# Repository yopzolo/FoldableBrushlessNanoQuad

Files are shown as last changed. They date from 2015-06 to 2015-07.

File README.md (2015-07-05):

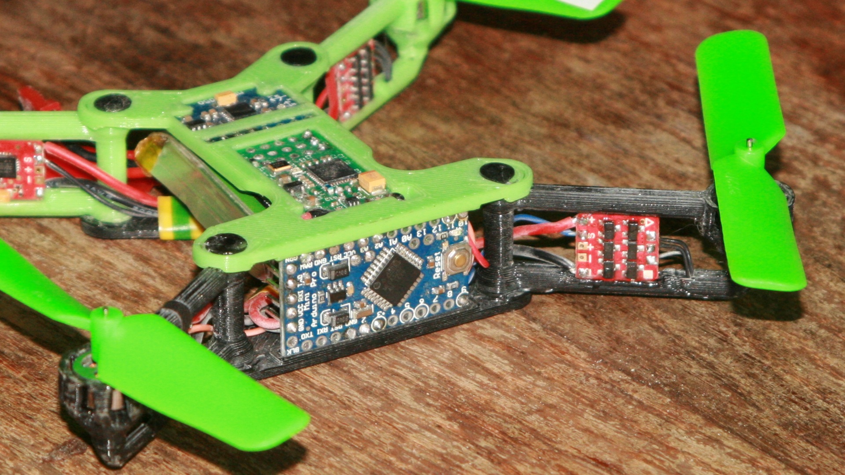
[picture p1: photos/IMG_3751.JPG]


## BOM
* [Arduino uno 3.3V / 8MHz](http://www.amazon.fr/gp/product/B00KMMF4TI?psc=1&redirect=true&ref_=oh_aui_detailpage_o07_s00)
* [MPU6050](http://www.amazon.fr/gp/product/B00E1EQXL6?psc=1&redirect=true&ref_=oh_aui_detailpage_o03_s00)
* [R410X](https://www.hobbyking.com/hobbyking/store/uh_customerShowOrderDetails2.asp?idOrder=20011845025)
* 4 X [Mi-3A](https://www.hobbyking.com/hobbyking/store/__44697__SuperMicro_Systems_Brushless_ESC_3A_Mi_3A.html)
* 4 X [hexTronik 2 gram Brushless Outrunner 7700kv](https://www.hobbyking.com/hobbyking/store/__7230__hexTronik_2_gram_Brushless_Outrunner_7700kv.html)
* 3020 propellers ( [Vl](https://www.hobbyking.com/hobbyking/store/%5F%5F40028%5F%5F3020%5FPropellers%5FGreen%5FL%5FH%5FRotation%5F5Pcs%5FBag%5F.html) [Vr](https://www.hobbyking.com/hobbyking/store/%5F%5F40029%5F%5F3020R%5FPropellers%5FGreen%5FR%5FH%5FRotation%5F5Pcs%5FBag%5F.html) [Or](https://www.hobbyking.com/hobbyking/store/%5F%5F41096%5F%5F3020R%5FPropellers%5FOrange%5FR%5FH%5FRotation%5F5Pcs%5FBag%5F.html) [Ol](https://www.hobbyking.com/hobbyking/store/%5F%5F41095%5F%5F3020%5FPropellers%5FOrange%5FL%5FH%5FRotation%5F5Pcs%5FBag%5F.html) [Br](https://www.hobbyking.com/hobbyking/store/%5F%5F40027%5F%5F3020R%5FPropellers%5FBlack%5FR%5FH%5FRotation%5F5Pcs%5FBag%5F.html) [Bl](https://www.hobbyking.com/hobbyking/store/%5F%5F40026%5F%5F3020%5FPropellers%5FBlack%5FL%5FH%5FRotation%5F5Pcs%5FBag%5F.html) )
* Silicon Wire [Black](https://www.hobbyking.com/hobbyking/store/%5F%5F10936%5F%5FTurnigy%5FPure%5FSilicone%5FWire%5F24AWG%5F1mtr%5FBlack.html) [Red](https://www.hobbyking.com/hobbyking/store/%5F%5F10937%5F%5FTurnigy%5FPure%5FSilicone%5FWire%5F24AWG%5F1mtr%5FRed.html)
* Batteries ( 1S < 20g ) - [300mAh](https://www.hobbyking.com/hobbyking/store/%5F%5F20384%5F%5FTurnigy%5Fnano%5Ftech%5F300mah%5F1S%5F35%5F70C%5FLipo%5FPack%5FFits%5FNine%5FEagles%5FSolo%5FPro%5F100%5F.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) [750mAh](https://www.hobbyking.com/hobbyking/store/%5F%5F20386%5F%5FTurnigy%5Fnano%5Ftech%5F750mah%5F1S%5F35%5F70C%5FLipo%5FPack%5FFits%5FNine%5FEagles%5FSolo%5FPro%5F180%5F.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)

# Calibrating and Printing

## micro_quad_brushless.scad needs 3 files

* constants.scad - printer constants
* components.scad - electronic component mocks
* componentsTest.scad - display and print test stubs for electronics and motors

## Adjust the params to fit your printer and electronic components

0. adjust printer constants
0. adjust electronic component mocks
0. render, export, slice, print and test with componentsTest.scad

## Reposition electronic components
if new size made them out of bound you must edit the copter frame micro_quad_brushless.scad to Reposition them

## Print
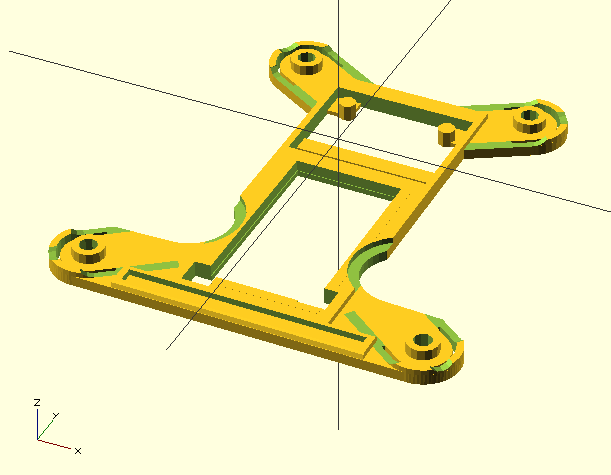
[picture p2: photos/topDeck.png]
Top Deck

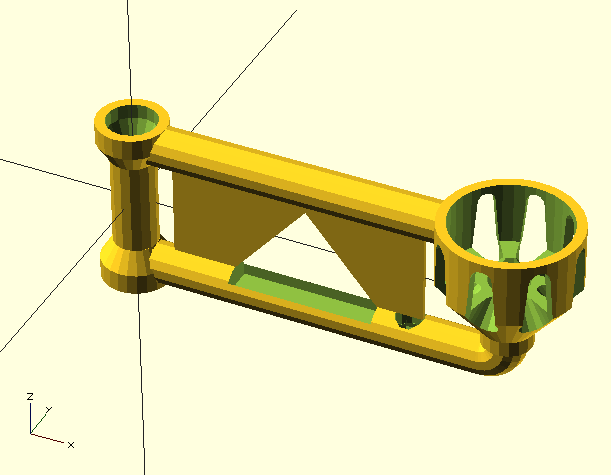
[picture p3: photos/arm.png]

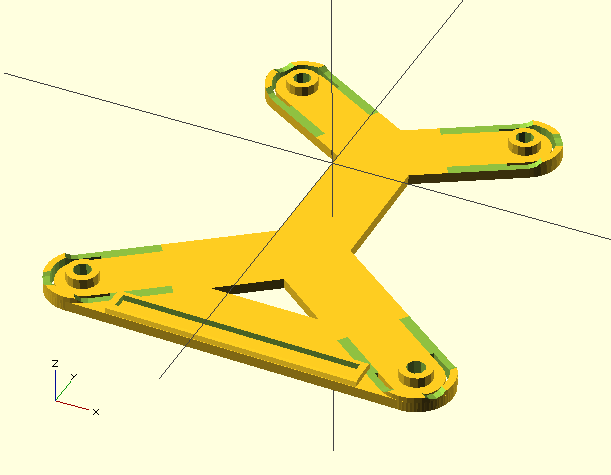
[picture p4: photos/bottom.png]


The safest order to validate prints is

0. top deck
0. One arm
0. the rest (3 arms and bottom)

## Assemble
Assembly pictures will come

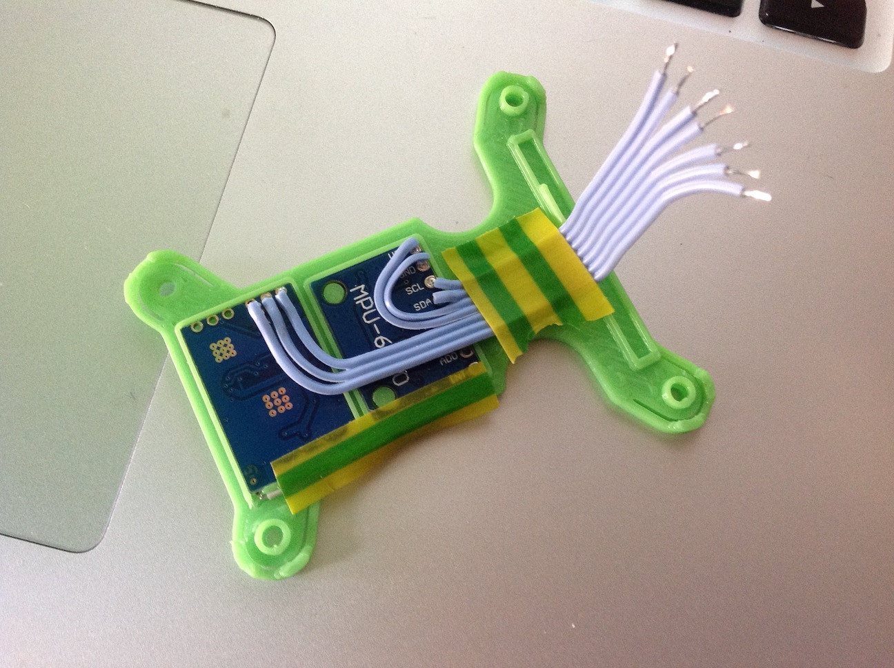
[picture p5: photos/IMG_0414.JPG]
0. use tiny wires for gyro and receiver (I used recylcled ribon), glue them to the frame after soldering 
0. use silicon wires to power the ESC (I used24AWG), power harness is taped to the bottom
0. place arms in closed position
0. use filament and weld it trough the arms

## Flashing Multiwii
You'll need a modified version of multiwii to run at 8Mhz

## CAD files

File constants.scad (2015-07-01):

INCH = 25.4;

tightFitThickness = .3; //space between to parts that must assemble

minimumThicknessHV = [.5,.3]; // minimal Wall,Floor thickness recommend to use [extrusion_width,layer_height]
strongThicknessHV = [2*minimumThicknessHV[0],5*minimumThicknessHV[1]]; // Wall,Floor thickness for strong parts recommend 2 walls, 5 layers

pinRad = 1.30; //radiant of the filament used to attach the arms. tested for 1.75 filament on reprap huxley

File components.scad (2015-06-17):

include <constants.scad>

*arduinoMock();
*motorMock();
*gyroMock();


// Main Arduino pro micro
arduinoSize = [34,2.3,18]; //[34,2.3,18]; ok values

module arduinoMock(){
		translate([0,0,arduinoSize[2]/2])cube(arduinoSize,center = true);	

		for (x = [0:12], y=[-1,1]) {
			*%translate([-arduinoSize[0]/2+(x+3/4)*INCH/10, 0, arduinoSize[2]/2+y*(arduinoSize[2]/2-INCH/20)])rotate([90,0,0])cylinder(r=INCH/30, h=arduinoSize[1]+.2,center = true);
		}
}

module arduinoHull(){
	clipThickness = .9;
	
	intersection() {
		translate([-arduinoSize[0]/2-strongThicknessHV[0],-arduinoSize[1]/2-strongThicknessHV[1],0])cube([arduinoSize[0]+2*strongThicknessHV[0], 2*strongThicknessHV[1]+arduinoSize[1], clipThickness]);
		translate([0,0,-arduinoSize[1]+2*clipThickness])rotate([0, 90, 0])cylinder(r=arduinoSize[1], h=arduinoSize[0]+2*strongThicknessHV[1]-.001,center = true);
	}

	//TODO remove after test print
	*translate([INCH/10,-arduinoSize[1]/2-minimumThicknessHV[0],0])cube([3/10*INCH,2*minimumThicknessHV[0]+arduinoSize[1],INCH/10]);
}

// gyro / acc

gyroSize=[20.5,16,1.8];
gyroFullThickness = 2.4;
gyroHolePadding=1.5;
gyroHoleRad = 1.25;

module gyroMock(){
	difference(){
		union() {
			translate([0,0,gyroFullThickness/2])cube(gyroSize+[0,0,gyroFullThickness-gyroSize[2]],center = true);

			

			for (x = [0:7]) {
				%translate([-gyroSize[0]/2+(x+1/2)*INCH/10, gyroSize[1]/2-INCH/20, gyroSize[2]/2])cylinder(r=INCH/30, h=gyroSize[2]+.2,center = true);
			}
		}
		for (i = [-1,1]) {
			translate([-i*(gyroSize[0]/2-gyroHoleRad-gyroHolePadding),-gyroSize[1]/2+gyroHoleRad+gyroHolePadding,0])cylinder(r=gyroHoleRad, h=gyroFullThickness+.1);
			translate([-i*(gyroSize[0]/2-gyroHoleRad),-gyroSize[1]/2+gyroHoleRad/2+gyroHolePadding,gyroFullThickness/2+gyroSize[2]/2])cube([gyroHoleRad+gyroHolePadding,gyroHoleRad+gyroHolePadding,gyroFullThickness-gyroSize[2]],center = true);
			translate([-i*(gyroSize[0]/2-gyroHoleRad/2-gyroHolePadding),-gyroSize[1]/2-gyroHoleRad/2+gyroHolePadding,gyroFullThickness/2+gyroSize[2]/2])cube([gyroHoleRad+gyroHolePadding,gyroHoleRad+gyroHolePadding,gyroFullThickness-gyroSize[2]],center = true);
			translate([-i*(gyroSize[0]/2-gyroHolePadding+gyroHoleRad/2),-gyroSize[1]/2-gyroHoleRad/2+gyroHolePadding,gyroFullThickness/2+gyroSize[2]/2])cube([gyroHoleRad+gyroHolePadding,gyroHoleRad+gyroHolePadding,gyroFullThickness-gyroSize[2]],center = true);

		}
		translate([0,gyroSize[1]/2-INCH/10-INCH/20,gyroFullThickness/2+gyroSize[2]/2])cube([gyroSize[0],INCH/10,gyroFullThickness-gyroSize[2]],center = true);


	}
}

module gyroHull(){
	*translate([0,0,strongThicknessHV[1]/2])cube([25,20,strongThicknessHV[1]], center = true);
		translate([0,0,gyroFullThickness/2-0.01])cube(gyroSize+2*strongThicknessHV[0]*[1,1,0]+[0,0,gyroFullThickness-gyroSize[2]-0.1,1], center = true);
		
		for (i = [-1,1]) {
			translate([-i*(gyroSize[0]/2+i*gyroHoleRad-INCH/20+i*minimumThicknessHV[0]/2),gyroSize[1]/2-gyroHoleRad-INCH/20-minimumThicknessHV[0]/2,gyroSize[2]-0.1])cube([2*gyroHoleRad+minimumThicknessHV[0],2*gyroHoleRad+minimumThicknessHV[0],minimumThicknessHV[1]]);
		}
}


// receiver

rxSize=[15.5,28,1.6];
rxFullThickness = 2.4;
rxAntennaSize=[2,2,rxFullThickness-2*minimumThicknessHV[1]];

module rxMock(){
	//difference() {
		//union() {
			translate([0,0,rxFullThickness/2-0.01])cube(rxSize+[-minimumThicknessHV[0]/2,-minimumThicknessHV[0]/2,rxFullThickness-rxSize[2]],center = true);
			translate([0,0,rxFullThickness-rxSize[2]/2])cube(rxSize,center = true);
		//}
		*translate([0, rxSize[1]/2, rxFullThickness/2-rxSize[2]/2])cube([rxSize[0],1,rxFullThickness-rxSize[2]] , center = true);
		*translate([rxSize[0]/2-5, rxSize[1]/2, rxFullThickness/2-rxSize[2]/2])cube([3, 2, rxFullThickness-rxSize[2]], center= true);
		*translate([rxSize[0]/2-5, -rxSize[1]/2, rxFullThickness/2-rxSize[2]/2])cube([3, 2, rxFullThickness-rxSize[2]], center= true);
//	}
	#translate([-rxSize[0]/2-rxAntennaSize[0]-minimumThicknessHV[1],-rxSize[1]/2-minimumThicknessHV[1]/2-rxAntennaSize[0],-0.01])cube([2*rxAntennaSize[0],2*rxAntennaSize[0],rxFullThickness]);
	#translate([+rxSize[0]/2-rxAntennaSize[0],-rxSize[1]/2-minimumThicknessHV[1],-.01])cube([2*rxAntennaSize[0],2*rxAntennaSize[0],rxFullThickness]);

}


module rxHull(){
 	translate([0,0,rxFullThickness/2-0.01])cube(rxSize+[2*strongThicknessHV[1],2*strongThicknessHV[1],rxFullThickness-rxSize[2]-0.01],center = true);
}

// esc's

escSize=[15,3.5,11.8];

// batery

batSize = [24,43,9];

// motors

motorRHTop = [6,5.5];
motorRHMiddle = [3.75,5];
motorRHBottom = [2.10,8];
motorRHPin = [.5,9];

motorRH = [max(motorRHTop[0],motorRHBottom[0]),motorRHBottom[1]+motorRHTop[1]];

module motorMock(){
	union() {
	translate([0,0,0])cylinder(r=motorRHBottom[0], h=motorRHBottom[1]);
	intersection() {
		translate([0,0,motorRHBottom[1]-motorRHMiddle[1]])cylinder(r1=motorRHBottom[0],r2=motorRHMiddle[0], h=motorRHMiddle[1]);
		translate([-motorRHBottom[0]+minimumThicknessHV[0],0,0])cube([2*motorRHBottom[0]-2*minimumThicknessHV[0],motorRHTop[0],motorRH[1]]);
	}
	//difference() {
		translate([0,0,motorRHBottom[1]-strongThicknessHV[0]])cylinder(r=motorRHTop[0], h=motorRHTop[1]+strongThicknessHV[0]+.01);
	//	#translate([0,0,motorRHBottom[1]-strongThicknessHV[0]-.01])cylinder(r=motorRHTop[0]-strongThicknessHV[1], h=strongThicknessHV[0]);	
	//}

	translate([0,0,motorRHBottom[1]+motorRHTop[1]])cylinder(r=motorRHPin[0], h=motorRHPin[1]);
	}
}

module motorHull(){
	ventHoleRad = 2*3.14*motorRH[0]/16-minimumThicknessHV[0];
	union() {
		difference() {
			union() {
				cylinder(r=motorRHBottom[0]+minimumThicknessHV[0], h=motorRHBottom[1]);
				translate([0,0,motorRHBottom[1]-motorRHMiddle[1]-2*strongThicknessHV[0]])cylinder(r1=motorRHBottom[0],r2=motorRH[0]+strongThicknessHV[0], h=motorRH[0]);
				translate([0,0,motorRHBottom[1]-strongThicknessHV[0]])cylinder(r=motorRH[0]+strongThicknessHV[0], h=motorRHTop[1]+strongThicknessHV[0]);
		}
			rotate([0, 0, -90])
			for (a = [45:45:315]) {
					hull() {
						translate([0,0,motorRH[1]])rotate([140, 0, a])cylinder(r1=0,r2=ventHoleRad, h=2*motorRH[0]);	
						translate([0,0,motorRH[1]-strongThicknessHV[1]-ventHoleRad])rotate([90, 0, a])cylinder(r1=0,r2=ventHoleRad, h=2*motorRH[0]);	
					}
			}
		}

		
	}
	
}

// utilities

module unionDiff(){
	difference() {
		union() {
			for (i = [0:$children-2]) {
				children(i);
			}
		}
		children($children-1);
	}
}

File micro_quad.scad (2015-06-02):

//micro quad
//include <Libs.scad>
INCH = 25.4;

propDH = [3*INCH,5];

motorCenters= [1.8*INCH,1.7*INCH]; //45.2,40.64
motorDH=[10,14];
motorWeigth=2;

motorPropTrust=36;

rxSize=[21,14,2];
rxWeight=2;

gyroSize=[20.32,15,4];
gyroWeight=2;

arduinoSize=[34,1.8,18];
arduinoWeight=3;

fcSize=[0,0,0];
fcWeigth=0;

escSize=[3.4,12.9,11.6];
escWeigth=.6; //0.36; j'ajoute le poids des fils ici

batSize=[24,43,9];
batWeigth=19;

echo ("diametre des hélices : ", propDH[0], "mm");

printSize = [motorDH[0]+2*motorCenters[0], motorDH[0]+2*motorCenters[1], 60];
echo ("class : " , 2*sqrt(pow(motorCenters[0],2)+pow(motorCenters[1],2)));
echo ("Lxlxh moteur a moteur : ", printSize, "mm" );
*%cube(printSize,center=true);

globalSize = [propDH[0]+2*motorCenters[0], propDH[0]+2*motorCenters[1], propDH[1]+motorDH[1]];
echo ("Lxlxh hors tout : ", globalSize, "mm");
translate([0,0,(propDH[1]-motorDH[1])/2])
*%cube(globalSize, center=true);

echo ("poids total : ", 4*motorWeigth + 4*escWeigth + fcWeigth + batWeigth, "g");
echo ("poids limite : ", 4/3*motorPropTrust, "g");
echo ("trust total : ", 4*motorPropTrust, "g");


for(x = [-1,1],y=[-1,1]){
	translate([x*motorCenters[0], y*motorCenters[1], propDH[1]/2])
	%color("red")cylinder(r=propDH[0]/2, h=propDH[1], center=true);

	translate([x*motorCenters[0], y*motorCenters[1], -motorDH[1]/2])
	cylinder(r=motorDH[0]/2, h=motorDH[1],center=true);	
}

cube(fcSize, center=true);

translate([0,-batSize[1]/2-arduinoSize[1]/2-1,-arduinoSize[2]/3])cube(arduinoSize,center=true);
translate([0,0,0])cube(gyroSize,center=true);
translate([0,rxSize[1]/2+gyroSize[1]/2+1,0])cube(rxSize,center=true);


translate([0,0,-batSize[2]])
cube(batSize,center=true);

for(x = [-1,1],y=[-1,1]){
	translate([x*(batSize[0]+escSize[0]+2)/2, y*(batSize[1]/2-escSize[1]), -batSize[2]])
	cube(escSize,center=true);
}


//tmp futur micro 2g

module arm(){
	cylinder(r=1.75, h=9,$fn=20);
	translate([0,0,9])cylinder(r=5, h=4.8,$fn=40);

}
translate([100,0 ,0 ]){
arm();
}

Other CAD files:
micro_quad_brushless.scad
componentsTest.scad

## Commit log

2015-06-02 commit initial
    [arm.stl, arm_vented.stl, body.stl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]
2015-06-09 réduction poid bottom, recul arduino pour laisser la place aux fils
    [arm.stl, arm_vented.stl, body.stl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]
2015-06-12 adaptation rx / allègement / adaptation esc
    [arm.stl, arm_vented.stl, body.stl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]
2015-06-14 vbat monitoring
    [config.h]
2015-06-15 increased socket rad at joint point
    [components.scad, componentsTest.scad, micro_quad_brushless.scad]
2015-06-15 arm fit adjustment
    [constants.scad, micro_quad_brushless.scad]
2015-06-16 updated scoket to fit in new size
    [micro_quad_brushless.scad]
2015-06-16 fold enhancement + arm printability
    [components.scad, micro_quad_brushless.scad]
2015-06-16 ajout ignore des exports
2015-06-17 all compoonents test by default
    [componentsTest.scad]
2015-06-17 reverse rx direction
    [components.scad, micro_quad_brushless.scad]
2015-06-29 export status
    [micro_quad_brushless.scad]
2015-07-01 comment on constants + rationalisation of values
    [constants.scad]
2015-07-05 comments + READMI
    [config.h, micro_quad_brushless.scad]
2015-07-06 suppression de multiwii dans le projet
    [config.h]
2015-07-06 ajout de multiwii en submodule
2015-08-18 remove old files
    [microQuadShape.dxf]
